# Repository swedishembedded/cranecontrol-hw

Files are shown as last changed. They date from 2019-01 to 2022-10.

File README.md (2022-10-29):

# CraneControl Schematic and PCB

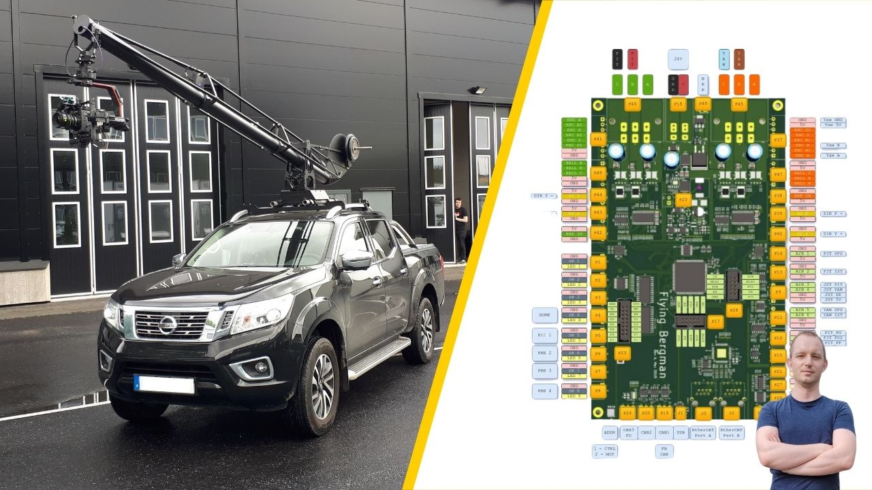
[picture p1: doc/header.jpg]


**Electronic hardware for controlling a vehicle mounted movie production crane**

	Copyright (c) 2019-2022 Martin Schröder, All rights reserved.

- Connect with me on LinkedIn: https://www.linkedin.com/in/martinschroder/
- Connect by email: martin.schroder@swedishembedded.com

This repository contains electical schematic and pcb layouts for boards that
can be used to control a movie production camera crane.

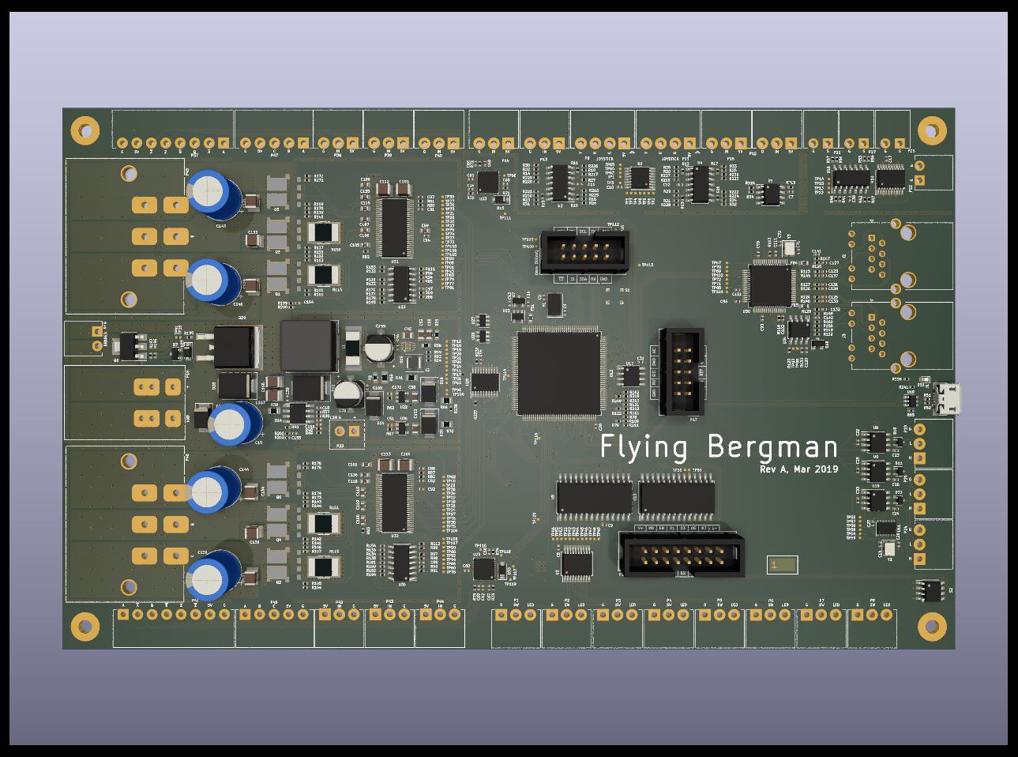
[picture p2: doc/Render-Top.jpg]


What does such a crane look like in practice? Well here is CraneControl boards
providing HMI and dual motor control function to FlyingBergman movie production
crane (click on images to watch the video):

[FlyingBergman](http://www.youtube.com/watch?v=k-2InPx5LMA
"FlyingBergman")

[FlyingBergman](http://www.youtube.com/watch?v=5sOf54V7gs8
"FlyingBergman on land")

[FlyingBergman](http://www.youtube.com/watch?v=lv9wT3cRuf8
"FlyingBergman at sea")

[FlyingBergman](https://flyingbergman.se) crane is best known for being used for filming all car scenes in
2022 Netflix series "Clark".

[FlyingBergman](http://www.youtube.com/watch?v=Xm6EU1w8b1s
"Clark")

If you are a movie producer and would like to order finished product then send
an email to info@swedishembedded.com and ask for more information. The complete
FlyingBergman setup also includes the crane assembly, HMI control panel for
mounting inside the vehicle and all necessary electronics.

## CraneControl platform

FlyingBergman is only one specific application of crane control hardware
design. CraneControl was originally designed to be a versatile solution capable
of advanced features like field oriented control of 2 60V PMSM motors at the
same time using the same microcontroller. It was also designed to provide
modern communication options like CAN-FD and EtherCAT.

In the case of FlyingBergman only a subset of these features was used - meaning
there is a lot of room to epand the use of this hardware for achieving more
complex control tasks in an industrial environment.

## Block diagram

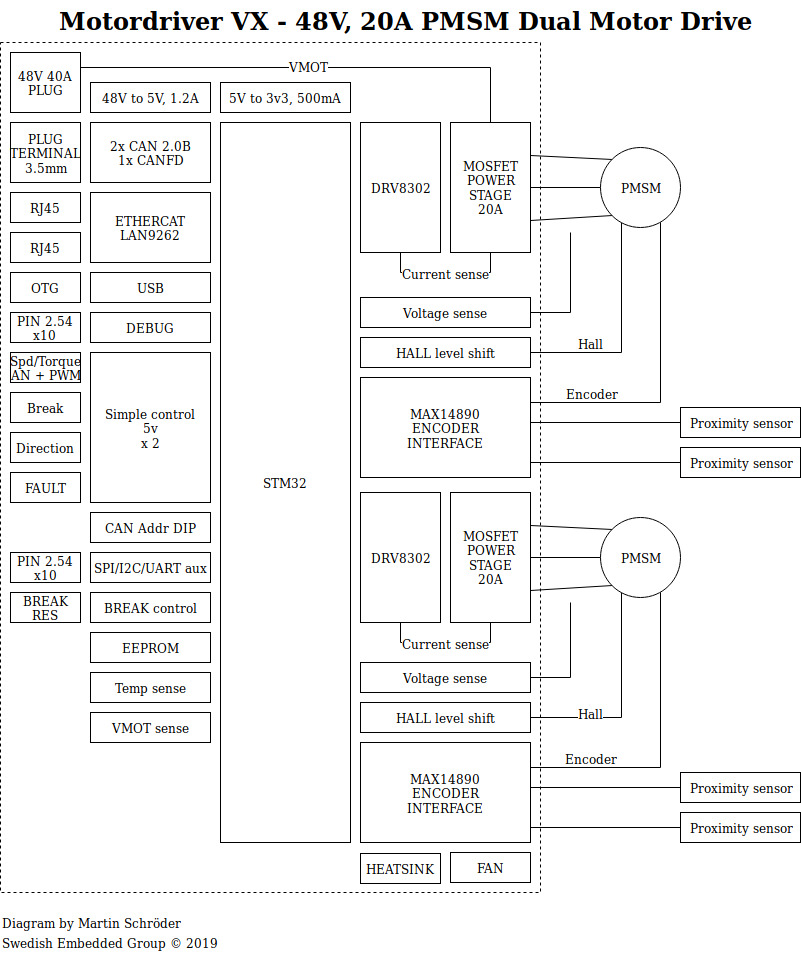
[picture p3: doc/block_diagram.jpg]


## Schematic PDF

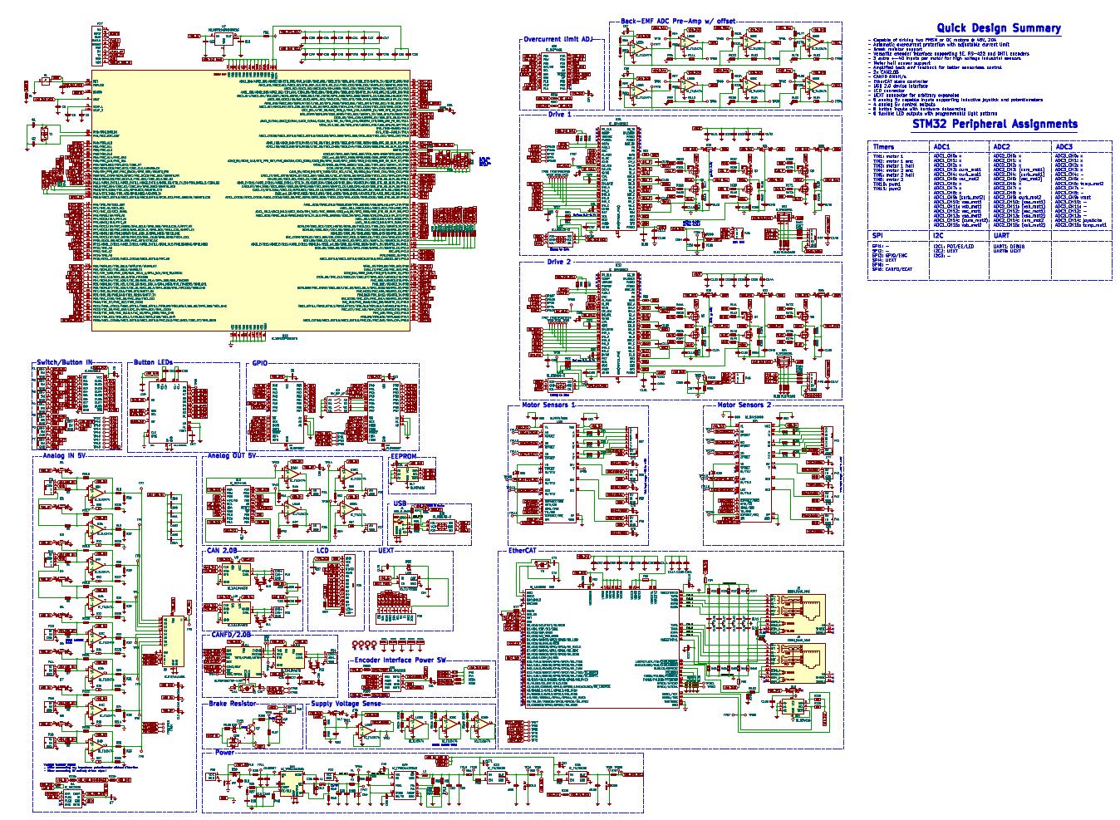
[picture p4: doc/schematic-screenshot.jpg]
Schematic


## Who is this for

This repository is for you if:

- You are a student of embedded systems courses at swedishembedded.com
  (https://swedishembedded.com/tag/training).

- You are building industrial control solutions and you would like to add
  support for advanced motor control (in this case you can also contract this
  task to Swedish Embedded Consulting Group. Book a call here:
  https://swedishembedded.com/book-call)

- You are simply curious about designing practical hardware and would like to
  learn from this project.

## License

You may use this design as inspiration for other designs as long as you develop
schematic and layout by yourself. You may also use this design as learning
materials for study.

If you would like to build a commercial product using this design then you can
contract Swedish Embedded Consulting Group to implement a specialized
hardware/software solution for you (send and email to
info@swedishembedded.com).

## Building

To generate gerbers for this design from command line you can use kibot
(https://github.com/INTI-CMNB/KiBot) with provided 'motordriver-2x.kibot.yaml'
file in this repository.

You can also edit this design in KiCad (version 6.0 or above).

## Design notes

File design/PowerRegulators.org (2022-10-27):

#+TITLE: PowerRegulators

* Main power regulator
This regulator is designed to handle up to 60V power input.

#+BEGIN_SRC octave :results output
% TPS54360 design

vout = 12;
vin = 60;
iout = 3.5;
rls = 10e3;
rdc = 36.8e-3;
vstart = 17;
vstop = 14;
lo = 33e-6;
dcj = 380e-12;
voripple = 0.005;
cout = 100e-6;
resr = 25e-3;
ioh = 2.625;
iol = 0.875;
fsw_chosen = 1500e3;
cin = 4.4e-6;
vf = 0.81;
rt_chosen = 137e3;

rdson = 92e-3;
dmax = 0.9;
i1 = 1.2e-6;
ihys = 3.4e-6;
vena = 1.2;
fdiv = 8;
voutsc = 0.1;
ton = 135e-9;
icl = 4.7;
kind = 0.3;
diout = 1.75;
dvout = 0.02;
vpeak = dvout + vout;
vi = vout;
gmps = 12;
gmea = 350e-6;
vref = 0.8;

% equation 1
vin_min = (vout + vf + rdc + iout)/0.99 + rdson * iout - vf;
% equation 2
vout_max = dmax * (vin_min - iout * rdson + vf) - vf + iout * rdc;
% equation 3
rhs = rls * (vout - vref)/vref;
% equation 4
ruvloh = (vstart - vstop)/ihys;
% equation 5
ruvlol = vena / ((vstart - vena)/ruvloh + i1);
% equation 7
rt_fsw_chosen = 1000 * 101756 / ((fsw_chosen / 1000) ^ 1.008);
rt = rt_chosen;
% equation 8
fsw = 1000 * 92417 / ((rt / 1000) ^ 0.991);
% equation 6
tss = 1024 / fsw;
% equation 9
fsw_max_skip = (1/ton) * ((iout * rdc + vout + vf)/(vin - iout * rdson + vf));
% equation 10
fsw_shift = (fdiv / ton) * ((icl * rdc + voutsc + vf)/(vin - icl * rdson + vf));
% equation 11
lo_min = ((vin - vout)/(iout * kind)) * (vout / (vin * fsw));
iripple = (vout * (vin - vout))/(vin * lo * fsw);
il_rms = sqrt(iout ^ 2 + 1/12 * ((vout * (vin - vout)) / (vin * lo * fsw))^2);
il_peak = iout + iripple / 2;
cout_min_1 = (2 * diout)/(fsw * dvout);
cout_min_2 = lo * (ioh ^ 2 - iol ^ 2)/(vpeak ^ 2 - vi ^ 2);
cout_min_3 = (1 / (fdiv * fsw)) * 1 / ((vout * voripple) / iripple);
cout_min = min([cout_min_1, cout_min_2, cout_min_3]);
resr_max = (vout * voripple) / iripple;
icout = (vout * (vin - vout))/(sqrt(12) * vin * lo * fsw);
pd = ((vin - vout) * iout * vf) / vin + (dcj * fsw * (vin + vf)^2)/2;
icirms = iout * sqrt((vout / vin_min) * (vin_min - vout)/vin_min);
dvin = (iout * 0.25)/(cin * fsw);

% equation 13
fp = iout / (2 * pi * vout * cout);
% equation 14
fz = 1 / (2 * pi * resr * cout);
fco_1 = sqrt(fp * fz);
fco_2 = sqrt(fp * fsw / 2);
fco = min(fco_1, fco_2);

r4 = ((2 * pi * fco * cout)/gmps) * (vout / (vref * gmea));
c5 = 1 / (2 * pi * r4 * fp);
c8_1 = (cout * resr) / r4;
c8_2 = 1 / (r4 * fsw * pi);
c8 = max(c8_1, c8_2);

printf('Rt for frequency %.2f: %.2f\n', fsw_chosen, rt_fsw_chosen);
printf('Switching frequency: %.2f\n', fsw);
printf('Rcomp: %f.2k, Ccomp: %fnf, Ccomp2: %f.2pf\n', r4 / 1e3, c5 / 1e-9, c8 / 1e-12)
printf('Rt: %.2fk\n', rt / 1e3)
printf('Cout_min: %.2fuf\n', cout_min / 1e-6)
printf('Rhs: %.2fk, Rls: %.2fk\n', rhs / 1e3, rls / 1e3)
printf('Ruvloh: %.2fk, Ruvlol: %.2fk\n', ruvloh / 1e3, ruvlol / 1e3)

#+END_SRC

#+RESULTS:
: Rt for frequency 1500000.00: 63982.33
: Switching frequency: 705117.97
: Rcomp: 12.198751.2k, Ccomp: 28.105922nf, Ccomp2: 204.939015.2pf
: Rt: 137.00k
: Cout_min: 1.22uf
: Rhs: 140.00k, Rls: 10.00k
: Ruvloh: 882.35k, Ruvlol: 62.81k

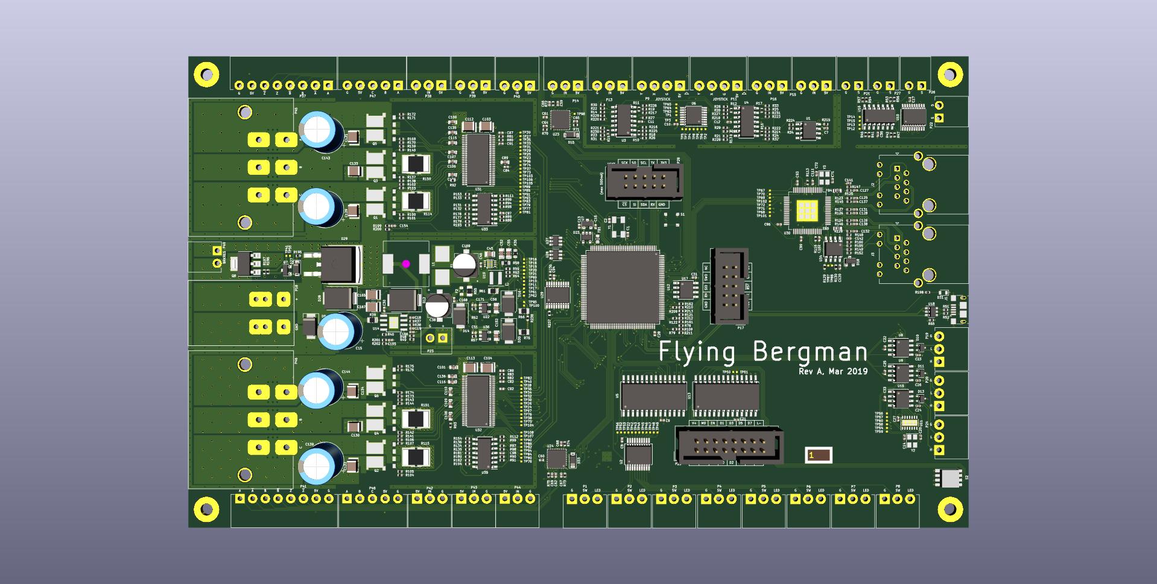
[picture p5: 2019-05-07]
doc/motordriver-2x.jpg

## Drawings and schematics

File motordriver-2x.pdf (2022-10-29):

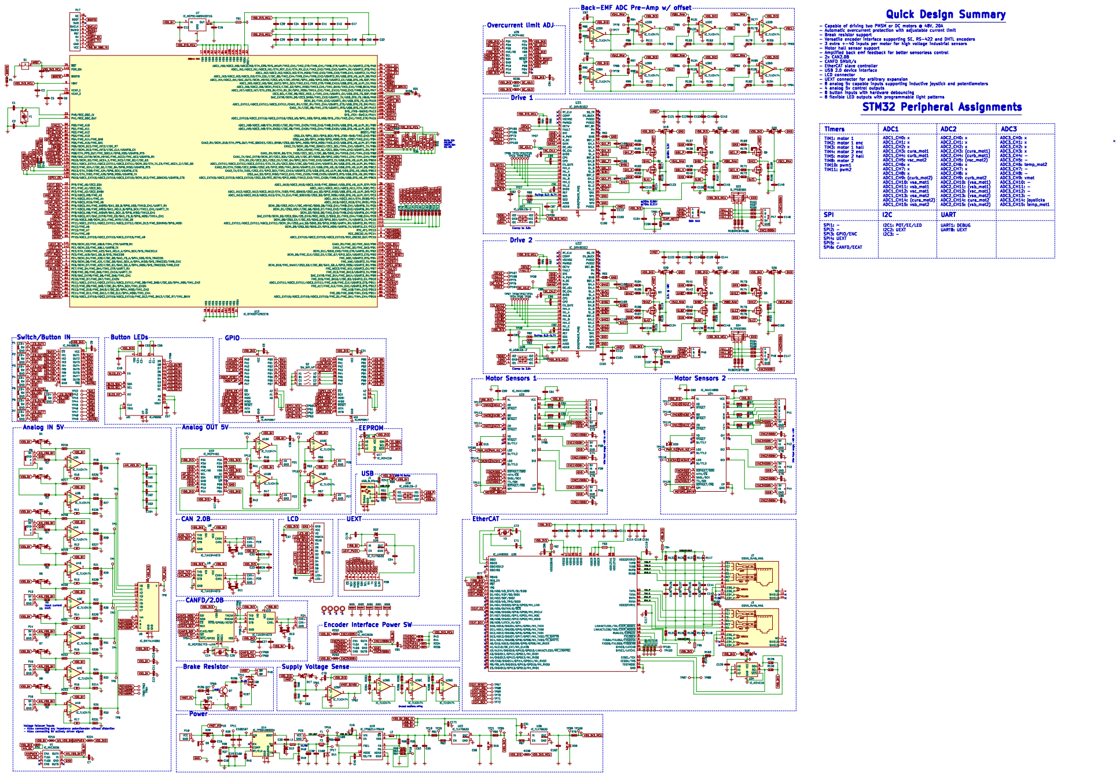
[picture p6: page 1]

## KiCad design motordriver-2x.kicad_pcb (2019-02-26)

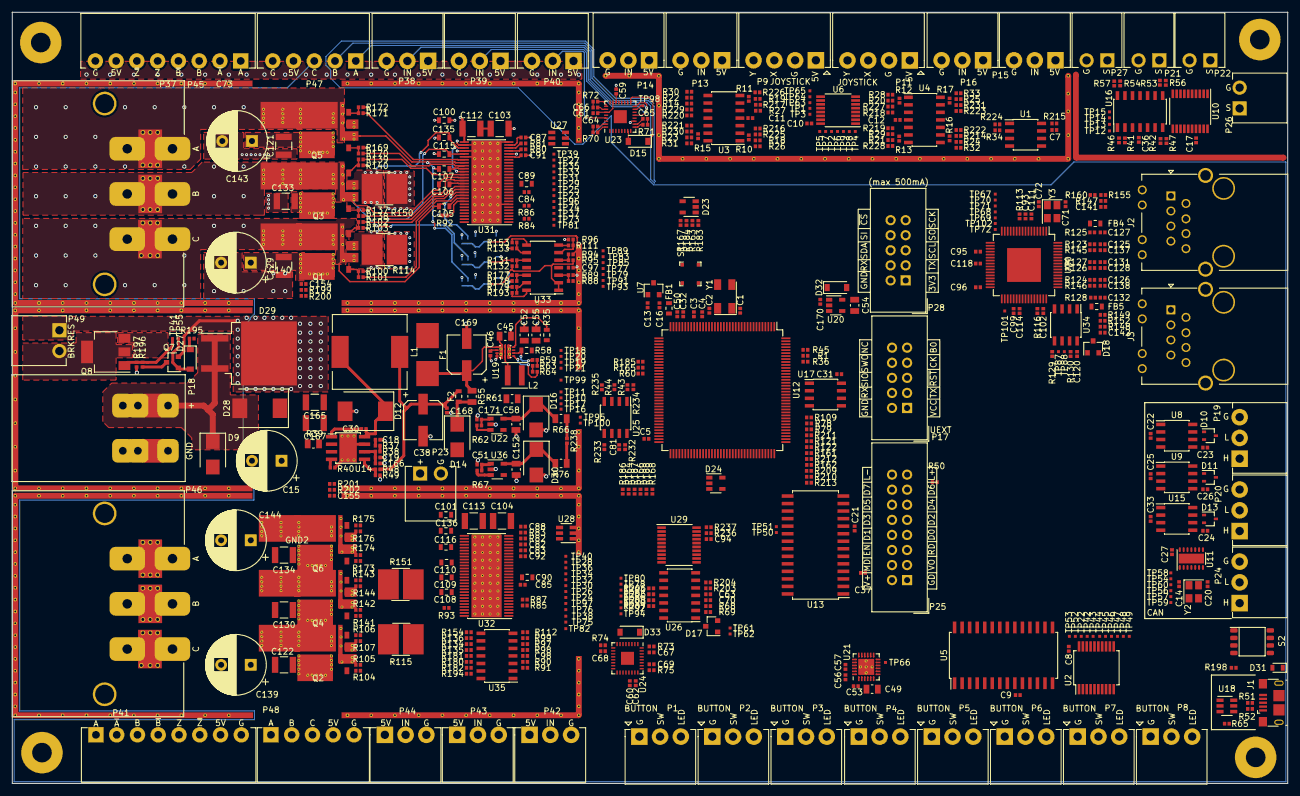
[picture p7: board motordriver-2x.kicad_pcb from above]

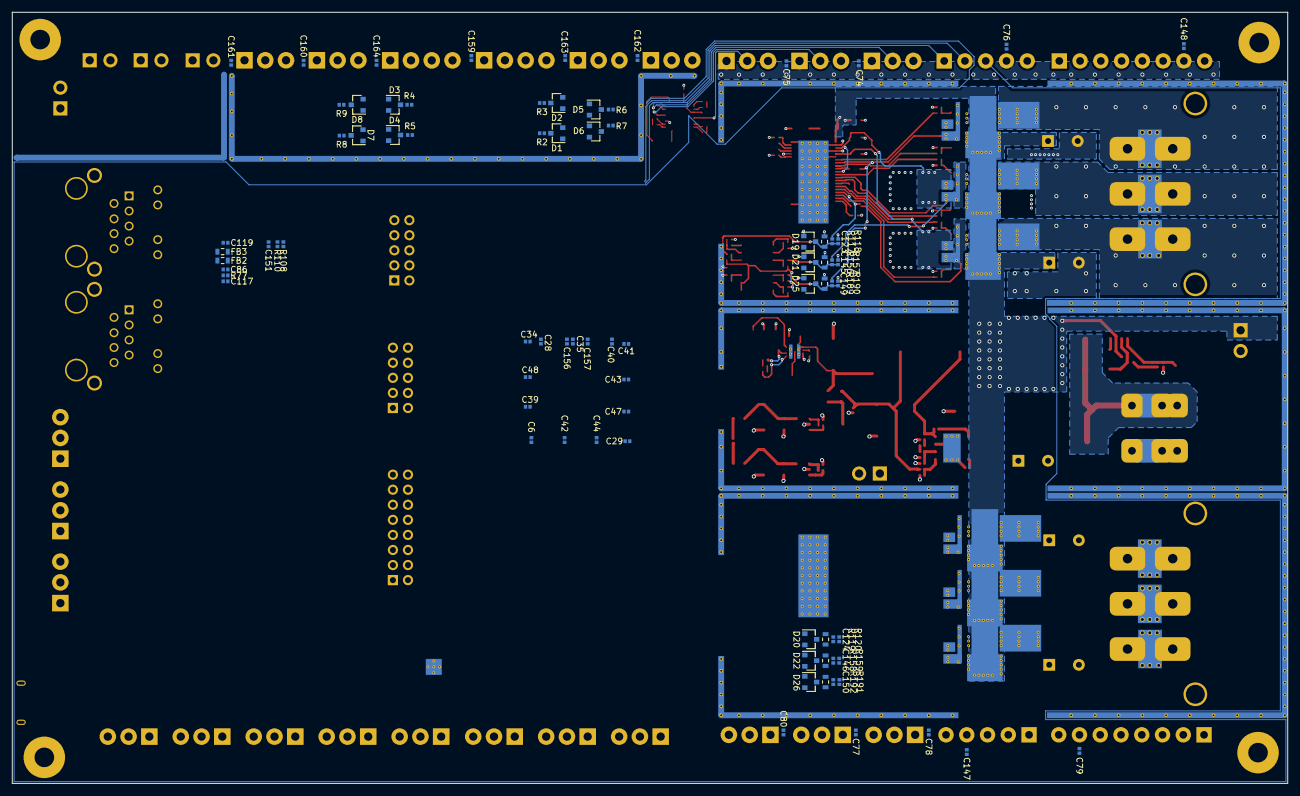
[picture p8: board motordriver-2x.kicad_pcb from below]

Board: 4 copper layers, 215.0 x 130.0 mm, 651 parts (79 on the bottom side), 453 nets.

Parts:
C1, C2, C14, C20, C71, C72, C125, C126, C127, C128, C131, C132, C137, C138: CAP_10pF_50V_0402; C_0402_1005Metric
C3, C4, C8, C9, C10, C11, C12, C16, C17, C21, C22, C23, C24, C25, C26, C27, C28, C29, C30, C31, C32, C33, C34, C35, C36, C39, C40, C41, C42, C43, C44, C46, C47, C48, C50, C59, C60, C61, C62, C63, C70, C82, C83, C86, C93, C94, C95, C96, C97, C98, C99, C102, C111, C114, C117, C118, C119, C120, C151, C154, C155, C156, C157: CAP_100nF_50V_0402; C_0402_1005Metric
C5, C6, C7, C13, C37, C51, C53, C56, C57, C73, C74, C75, C76, C77, C78, C79, C80, C81, C84, C85, C87, C88, C91, C92, C147, C148, C159, C160, C161, C162, C163, C164, C168, C170, C171: CAP_2.2uF_16V_0402; C_0402_1005Metric
C15, C139, C140, C143, C144: CAPP_220uF_63V_10x15_THT; CP_Radial_D10.0mm_P5.00mm
C18: CAP_27nF_16V_0402; C_0402_1005Metric
C19, C64, C65, C66, C67, C68, C69, C166: CAP_100pF_50V_0402; C_0402_1005Metric
C38, C169: CAPP_100uF_25V_6357; CP_Elec_6.3x5.7
C45, C49: CAP_10uF_25V_0805; C_0805_2012Metric
C52, C54, C55, C58, C152: CAP_22uF_10V_0805; C_0805_2012Metric
C89, C90: CAP_0.022uF_100V_0603; C_0603_1608Metric
C100, C101, C105, C106, C107, C108, C109, C110, C123, C124, C145, C146, C149, C150: CAP_100nF_100V_0603; C_0603_1608Metric
C103, C104, C112, C113, C121, C122, C129, C130, C133, C134, C165, C167: CAP_2.2uF_100V_1210; C_1210_3225Metric
C115, C116, C135, C136: CAP_1nF_100V_0603; C_0603_1608Metric
C141, C142: CAP_22nF_50V_0402; C_0402_1005Metric
D1, D2, D3, D4, D5, D6, D7, D8, D17, D18, D19, D20, D21, D22, D25, D26: D_BAT54S; SOT-23
D9: D_SMBJ48A; D_SMB
D10, D11, D13: D_ESDCAN03; SOT-323_SC-70
D12, D28: D_CDBC5100; D_SMC
D14: D_SMBJ12A; D_SMB
D15, D27, D32, D33: D_BAT54; D_SOD-123
D16, D30: D_SZ1SMB5913BT3G; D_SMB
D23, D24: D_TPD3E001; SOT-23-5
D29: D_STPS41H100; TO-263-2
D31: LED_RED_0603; LED_0603_1608Metric
F1: FUSE_3A_9750; Fuse_Littlefuse_9750
F2: FUSE_4A_0603; Fuse_0603_1608Metric
FB1, FB2, FB3, FB4, FB5: LB_220R_2A_0603; L_0603_1608Metric
GND1: GND_100X30
GND2, GND3: GND_MOTOR_DRIVER
GND4: GND_ANALOG_IN
GND5: GND_ANALOG_OUT
J1: USB_B_Micro; USB_Micro-B_GCT_USB3076-30-A
J2, J3: CONN_RJ45_MAG; RJ45_Tranformer
L1: L_33uH_4.2A_45mR; L_Wuerth_WE-PD-Typ-LS_1250x1250
L2: L_2.2uH_8A; L_Coilcraft_XxL4020
MT1, MT2, MT3, MT4: MOUNT_HOLE; MountingHole_3.2mm_M3_Pad
P1, P2, P3, P4, P5, P6, P7, P8: CONN_BUTTON
P9, P11: CONN_JOYSTICK
P13, P14, P15, P16, P38, P39, P40, P42, P43, P44: CONN_SENSOR
P17: CONN_DEBUG_2R; IDC-Header_2x05_P2.54mm_Vertical
P18: CONN_POWER_41A; PhoenixContact_Power41A_2,5_2-G-7,62_1x02_P7.62mm_Horizontal
P19, P20, P24: CONN_CAN
P21, P22, P26, P27: CONN_AN_OUT
P23: CONN_POWER_10A
P25: CONN_LCD
P28: CONN_UEXT
P37, P41: CONN_ENCODER
P45, P46: CONN_MOTOR; ANYTEK_7.62mm_2x_3P_32A
P47, P48: CONN_HALL
P49: CONN_BRKRES
Q1, Q2, Q3, Q4, Q5, Q6: Q_NMOS_2X_60V_63A; PowerPack-8x8-Dual
Q7: Q_PNP_BC856; SOT-23
Q8: Q_NMOS_BUK9875; SOT-223
R1, R2, R3, R4, R5, R6, R7, R8, R9, R38, R41, R42, R43, R44, R49, R53, R54, R60, R62, R63, R64, R67, R84, R85, R86, R87, R88, R89, R90, R91, R94, R95, R96, R97, R98, R99, R100, R103, R104, R107, R108, R110, R113, R116, R118, R120, R131, R132, R133, R134, R135, R136, R137, R140, R141, R144, R149, R157, R159, R160, R169, R172, R173, R176, R177, R178, R179, R180, R181, R182, R183, R184, R185, R186, R187, R188, R190, R192, R195, R196, R197, R199, R201, R203, R204, R205, R206, R207, R208: RES_10K_1%_0402; R_0402_1005Metric
R10, R11, R12, R13, R14, R15, R16, R17, R65, R147, R148: RES_0R_0402; R_0402_1005Metric
R18, R19, R20, R21, R22, R23, R24, R25: RES_1K5_1%_0402; R_0402_1005Metric
R26, R27, R28, R29, R30, R31, R32, R33, R36, R37, R45, R59, R80, R81, R82, R83, R129, R130: RES_3K_1%_0402; R_0402_1005Metric
R34, R214, R215, R216, R217, R218, R219, R220, R221, R222, R223, R224, R225, R226, R227, R228, R229, R230, R231, R232, R233, R234, R235, R236, R237, R238: RES_NOFIT_0402; R_0402_1005Metric
R35, R58: RES_147k_1%_0603; R_0603_1608Metric
R39, R55, R61, R66, R76: RES_10mOhm_1%; R_0805_2012Metric
R40, R48, R68, R117, R119, R156, R158, R189, R191: RES_137K_1%_0402; R_0402_1005Metric
R46, R47, R56, R57, R69, R111, R112, R153, R154, R163, R164, R165, R166, R167, R168, R193, R194: RES_5K_1%_0402; R_0402_1005Metric
R50, R198: RES_470R_1%_0402; R_0402_1005Metric
R51, R52, R101, R102, R105, R106, R138, R139, R142, R143, R170, R171, R174, R175: RES_22R_1%_0402; R_0402_1005Metric
R70, R71, R72, R73, R74, R75, R78, R79, R109, R121, R122, R152, R155, R161, R162, R209, R210, R211, R212, R213: RES_270R_1%_0402; R_0402_1005Metric
R77: RES_12.1K_1%_0402; R_0402_1005Metric
R92, R93: RES_1M_1%_0402; R_0402_1005Metric
R114, R115, R150, R151: RES_5mR_1%_10W; R_2818_7146Metric
R123, R124, R125, R126, R127, R128, R145, R146: RES_49.9_0.1%_0402; R_0402_1005Metric
R200, R202: RES_NTC_10K_402; R_0402_1005Metric
S1: SW_BTN_3.7x3.7; SW_PTS540
S2: SW_DIP_4P; SOIC127P670X145-8N
TP1, TP2, TP3, TP4, TP5, TP6, TP7, TP8, TP9, TP10, TP11, TP12, TP13, TP14, TP15, TP16, TP17, TP18, TP19, TP20, TP21, TP22, TP23, TP24, TP25, TP26, TP27, TP28, TP29, TP30, TP31, TP32, TP33, TP34, TP35, TP36, TP37, TP38, TP39, TP40, TP41, TP42, TP43, TP44, TP45, TP46, TP47, TP48, TP49, TP50, TP51, TP52, TP53, TP54, TP55, TP56, TP57, TP58, TP59, TP60, TP61, TP62, TP63, TP64, TP65, TP66, TP67, TP68, TP69, TP70, TP71, TP72, TP73, TP74, TP75, TP76, TP77, TP78, TP79, TP80, TP81, TP82, TP83, TP84, TP85, TP86, TP87, TP88, TP89, TP90, TP91, TP92, TP93, TP94, TP95, TP96, TP97, TP98, TP99, TP100, TP101, TP102: Test_Point; TestPoint_Pad_0.5x0.5mm
U1, U25: IC_MIC2026; SOIC-8_3.9x4.9mm_P1.27mm
U2: IC_MAX6818; SSOP-20_5.3x7.2mm_P0.65mm
U3, U4, U16, U26, U33, U35: IC_TLV2474; SOIC-14_3.9x8.7mm_P1.27mm
U5, U13: IC_MCP23S17; SOIC-28W_7.5x17.9mm_P1.27mm
U6: IC_SN74LV4051; TSSOP-16_4.4x5mm_P0.65mm
U7: IC_NCP51460SN33T1G; SOT-23
U8, U9, U15: IC_TJA1044GT3; SOIC-8_3.9x4.9mm_P1.27mm
U10, U29: IC_MCP4461; TSSOP-20_4.4x6.5mm_P0.65mm
U11: IC_MCP2517FD-xJHA; DFN-14-1EP_3x4.5mm_P0.65mm_EP1.65x4.25mm
U12: IC_STM32F429ZET6; LQFP-144_20x20mm_P0.5mm
U14: IC_TPS54360DDA; TI_SO-PowerPAD-8
U17, U34: IC_M24C16; SOIC-8_3.9x4.9mm_P1.27mm
U18, U27, U28: IC_USBLC6-2; SOT-23-6L
U19: IC_TPS62147RGXR; RGX_VQFN-11
U20, U22, U36: IC_TLV75533; SOT-23-5
U21: IC_LP55231; WQFN-24-1EP_4x4mm_P0.5mm_EP2.7x2.7mm_Thermal
U23, U24: IC_MAX14890; QFN-32-1EP_5x5mm_P0.5mm_EP2.20x2.20mm
U30: IC_LAN9252; TQFP-64-1EP_10x10mm_P0.5mm_EP5.7x5.7mm
U31, U32: IC_DRV8302; HTSSOP-56-PowerPAD_6.2x14.1mm_P0.5mm_EP3.61x6.35mm
Y1: XTAL_8Mhz_5032; Crystal_ABM3B_5032-4Pin_5.0x3.2mm
Y2: XTAL_20MHz_3225; Crystal_SMD_3225-4Pin_3.2x2.5mm
Y3: XTAL_25MHz_3225; Crystal_SMD_3225-4Pin_3.2x2.5mm

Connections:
AINPWEN: R224.2, U1.1, U12.12
AIN_OC: R34.1, U1.2, U5.21
AIN_VDD_5V: C159.1, C160.1, C161.1, C162.1, C163.1, C164.1, P9.1, P11.1, P13.1, P14.1, P15.1, P16.1, R215.1, U1.8
AP_RESET1: U5.25, U10.15
AP_SCL1: R45.1, U10.5, U12.139, U17.6, U21.9, U29.5
AP_SDA1: R36.1, U10.6, U12.137, U17.5, U21.8, U29.6
AP_WP1: U5.24, U10.14
BLED_EN: U12.58, U21.5
BLED_INT: U12.67, U21.7
BOOT0: P17.9, R1.2, U12.138
CANFD_CS: TP60.1, U11.13, U12.125
CANFD_INT: TP59.1, U11.4, U12.124
CANFD_MISO: TP70.1, U11.12, U12.127, U30.13
CANFD_MOSI: TP69.1, U11.11, U12.129, U30.17
CANFD_SCK: TP72.1, U11.10, U12.128, U30.19
CANFD_SOF: U11.3, U12.93
CAN_RX1: U8.4, U12.114
CAN_RX2: U9.4, U12.73
CAN_TX1: U8.1, U12.115
CAN_TX2: U9.1, U12.74
DC_CAL1: TP74.1, U12.89, U31.12
DC_CAL2: TP76.1, U12.90, U32.12
ECAT_CS: TP71.1, U12.126, U30.50
ECAT_IRQ: TP68.1, U12.92, U30.44
ECAT_RESET: TP67.1, U12.91, U30.11
EE_WEN: U12.140, U17.7
ENC1VDD5V: C73.2, C74.2, C75.2, C76.2, C148.1, P37.7, P38.1, P39.1, P40.1, P47.4, R232.1, U25.8
ENC2VDD5V: C77.2, C78.2, C79.2, C80.2, C147.1, P41.7, P42.1, P43.1, P44.1, P48.4, R233.1, U25.5
ENCA1: U12.110, U23.1
ENCA2: U12.81, U24.1
ENCB1: U12.133, U23.8
ENCB2: U12.82, U24.8
ENCCS1: U12.118, U23.4
ENCCS2: U12.86, U24.4
ENCMISO1: R121.1, U23.3
ENCMISO2: R122.1, U24.3
ENCMOSI1: R162.1, U23.6
ENCMOSI2: R209.1, U24.6
ENCOC1: R43.2, U5.22, U25.2
ENCOC2: R44.2, U5.23, U25.3
ENCPWEN1: R234.2, U12.69, U25.1
ENCPWEN2: R235.2, U12.70, U25.4
ENCSCK1: R78.1, U23.5
ENCSCK2: R79.1, U24.5
ENCSH1: U12.119, U23.28
ENCSH2: U12.80, U24.28
ENCZ1: U12.77, U23.24
ENCZ2: U12.85, U24.24
EN_GATE1: TP96.1, U12.117, U31.16
EN_GATE2: TP97.1, U12.116, U32.16
FAULT1: R86.1, U12.122, U31.6
FAULT2: R87.1, U12.123, U32.6
GA1_N: R102.2, U31.45
GA1_P: R101.2, U31.47
GAIN1: TP73.1, U12.53, U31.10
GAIN2: TP75.1, U12.55, U32.10
GB1_N: R139.2, U31.40
GB1_P: R138.2, U31.42
GC1_N: R171.2, U31.35
GC1_P: R170.2, U31.37
GHA2: R105.2, U32.47
GHB2: R142.2, U32.42
GHC2: R174.2, U32.37
GLA2: R106.2, U32.45
GLB2: R143.2, U32.40
GLC2: R175.2, U32.35
GND: C1.2, C2.2, C3.2, C4.2, C5.2, C6.2, C7.2, C8.2, C9.2, C10.1, C11.1, C12.1, C13.2, C14.1, C15.2, C16.2, C17.1, C18.2, C19.2, C20.2, C21.2, C22.1, C23.1, C24.1, C25.1, C26.1, C27.1, C28.2, C29.2, C31.1, C32.2, C33.2, C34.2, C35.2, C36.1, C37.2, C38.2, C39.2, C40.2, C41.2, C42.2, C43.2, C44.2, C45.2, C46.2, C47.2, C48.2, C49.2, C50.2, C51.1, C52.2, C54.2, C55.2, C57.2, C58.2, C59.2, C60.2, C61.2, C62.2, C63.2, C70.1, C71.1, C72.1, C73.1, C74.1, C75.1, C76.1, C77.1, C78.1, C79.1, C80.1, C81.2, C82.2, C83.2, C84.2, C85.2, C86.1, C87.2, C88.2, C91.2, C92.2, C93.2, C94.1, C95.2, C96.2, C97.1, C98.1, C99.2, C100.2, C101.2, C102.2, C103.2, C104.2, C111.2, C114.2, C115.2, C116.2, C117.1, C118.2, C119.2, C120.1, C121.2, C122.2, C123.2, C124.2, C125.1, C126.2, C127.1, C128.2, C129.2, C130.2, C131.1, C132.2, C133.2, C134.2, C135.2, C136.2, C137.1, C138.2, C139.2, C140.2, C141.2, C142.1, C143.2, C144.2, C145.2, C146.2, C147.2, C148.2, C149.2, C150.2, C151.2, C152.2, C154.1, C155.1, C156.1, C157.1, C159.2, C160.2, C161.2, C162.2, C163.2, C164.2, C165.2, C166.2, C167.2, C168.2, C169.2, C170.2, C171.1, D1.1, D2.1, D3.1, D4.1, D5.1, D6.1, D7.1, D8.1, D9.2, D10.3, D11.3, D12.2, D13.3, D14.2, D16.2, D17.1, D19.1, D20.1, D21.1, D22.1, D23.3, D24.3, D25.1, D26.1, D30.2, D31.1, GND1.1, GND2.1, GND3.1, GND4.1, GND5.1, J1.5, J1.6, J2.8, J2.9, J3.8, J3.9, P1.1, P2.1, P3.1, P4.1, P5.1, P6.1, P7.1, P8.1, P9.2, P11.2, P13.3, P14.3, P15.3, P16.3, P17.2, P18.2, P19.3, P20.3, P21.2, P22.2, P23.2, P24.3, P25.1, P25.16, P26.2, P27.2, P28.2, P37.8, P38.3, P39.3, P40.3, P41.8, P42.3, P43.3, P44.3, P47.5, P48.5, Q5.3, Q6.3, Q8.3, R1.1, R26.2, R27.2, R28.2, R29.2, R30.2, R31.2, R32.2, R33.2, R40.2, R41.2, R42.2, R49.2, R53.2, R54.2, R60.2, R64.2, R69.1, R77.2, R89.1, R91.1, R92.1, R93.1, R96.2, R99.2, R100.2, R103.2, R104.2, R107.2, R108.1, R110.1, R113.1, R114.1, R115.1, R116.1, R118.1, R120.1, R133.2, R136.2, R137.2, R140.2, R141.2, R144.2, R149.1, R150.2, R151.2, R157.1, R159.1, R160.1, R169.2, R172.2, R173.2, R176.2, R179.2, R182.2, R183.1, R184.1, R185.1, R186.1, R187.1, R188.1, R190.1, R192.1, R197.2, R200.2, R202.2, R204.1, R206.1, R208.1, R214.1, R225.1, R226.1, R227.1, R228.1, R229.1, R230.1, R231.1, S1.1, S1.2, S2.1, S2.2, S2.3, S2.4, U1.6, U2.10, U3.11, U4.11, U5.10, U5.15, U5.16, U5.17, U6.6, U6.7, U6.8, U7.3, U8.2, U8.8, U9.2, U9.8, U10.3, U10.4, U10.7, U10.8, U10.13, U10.16, U10.18, U11.7, U11.15, U12.16, U12.31, U12.38, U12.51, U12.61, U12.83, U12.94, U12.107, U12.120, U12.130, U13.10, U13.15, U13.16, U13.17, U14.7, U14.9, U15.2, U16.11, U17.1, U17.2, U17.3, U17.4, U18.2, U19.3, U19.4, U19.10, U19.11, U20.2, U21.4, U21.6, U21.10, U21.20, U21.21, U21.25, U22.2, U23.11, U23.33, U24.11, U24.33, U25.6, U26.11, U27.2, U28.2, U29.3, U29.7, U29.8, U29.13, U29.16, U29.18, U30.4, U30.41, U30.65, U31.7, U31.8, U31.28, U31.30, U31.32, U31.34, U31.57, U32.7, U32.8, U32.28, U32.30, U32.32, U32.34, U32.57, U33.11, U34.1, U34.2, U34.3, U34.4, U34.7, U35.11, U36.2
GPEX_CS: U12.136, U13.11
GPEX_INTA: TP50.1, U12.21, U13.20
GPEX_INTB: TP51.1, U12.22, U13.19
GPEX_MISO: R212.1, U13.14
GPEX_MOSI: R213.1, U13.13
GPEX_RESET: U12.49, U13.18
GPEX_SCK: R211.1, U13.12
GPIO_CS: U5.11, U12.88
GPIO_INTA: TP52.1, U5.20, U12.57
GPIO_INTB: TP53.1, U5.19, U12.87
GPIO_MISO: R161.1, U5.14
GPIO_MOSI: R210.1, U5.13
GPIO_RESET: U5.18, U12.56
GPIO_SCK: R109.1, U5.12
HALL_A1: D23.1, R163.2, R183.2, U12.134
HALL_A2: D24.1, R164.2, R186.2, U12.34
HALL_B1: D23.2, R167.2, R184.2, U12.135
HALL_B2: D24.2, R166.2, R187.2, U12.35
HALL_C1: D23.4, R165.2, R185.2, U12.46
HALL_C2: D24.4, R168.2, R188.2, U12.36
INHA1: TP23.1, U12.60, U31.17
INHA2: TP24.1, U12.96, U32.17
INHB1: TP29.1, U12.64, U31.19
INHB2: TP30.1, U12.97, U32.19
INHC1: TP33.1, U12.66, U31.21
INHC2: TP34.1, U12.98, U32.21
INLA1: TP25.1, U12.59, U31.18
INLA2: TP26.1, U12.43, U32.18
INLB1: TP31.1, U12.63, U31.20
INLB2: TP32.1, U12.75, U32.20
INLC1: TP35.1, U12.65, U31.22
INLC2: TP36.1, U12.76, U32.22
LCD_D0: P25.7, U13.1
LCD_D1: P25.8, U13.2
LCD_D2: P25.9, U13.3
LCD_D3: P25.10, U13.4
LCD_D4: P25.11, U13.5
LCD_D5: P25.12, U13.6
LCD_D6: P25.13, U13.7
LCD_D7: P25.14, U13.8
LCD_EN: P25.6, U13.23
LCD_LED: R50.2, U13.24
LCD_MDATA: P25.4, U13.21
LCD_READ: P25.5, U13.22
LCD_VO: P25.3, U29.9
LED_OUT1: P1.3, U21.19
LED_OUT2: P2.3, U21.18
LED_OUT3: P3.3, U21.17
LED_OUT4: P4.3, U21.16
LED_OUT5: P5.3, U21.15
LED_OUT6: P6.3, U21.14
LED_OUT7: P7.3, U21.13
LED_OUT8: P8.3, U21.12
MOC1: U12.50, U31.9
MOC2: U12.54, U32.9
MOCP_RESET: U5.26, U29.15
MOCP_WP: U5.27, U29.14
MOTOR1_BRKIN: D15.2, U12.68, U23.7
MOTOR2_BRKIN: D33.2, U12.42, U24.7
NRST: C4.1, P17.5, S1.3, S1.4, U12.25
unnamed: C1.1, U12.23, Y1.1
unnamed: C2.1, U12.24, Y1.3
unnamed: C5.1, U12.71
unnamed: C6.1, U12.106
unnamed: C14.2, U11.5, Y2.1
unnamed: C15.1, D28.1, R39.2, TP10.1
unnamed: C18.1, R37.2
unnamed: C20.1, U11.6, Y2.3
unnamed: C30.1, D12.1, L1.1, U14.8
unnamed: C30.2, U14.1
unnamed: C32.1, C50.1, FB1.2, U12.32, U12.33
unnamed: C46.1, U19.9
unnamed: C52.1, C55.1, L2.2, R35.1, R58.1, R61.2, TP19.1, U19.6
unnamed: C53.1, U21.1
unnamed: C53.2, U21.23
unnamed: C54.1, D32.2, P28.1, U20.5
unnamed: C56.1, U21.24
unnamed: C56.2, U21.2
unnamed: C57.1, U21.22
unnamed: C58.1, D16.1, R66.2, TP21.1, U22.5
unnamed: C63.1, D17.3, R68.2, R69.2, TP61.1, U26.3
unnamed: C64.1, R70.2
unnamed: C64.2, P37.2, U23.31
unnamed: C65.1, R71.2
unnamed: C65.2, P37.4, U23.10
unnamed: C66.1, R72.2
unnamed: C66.2, P37.6, U23.26
unnamed: C67.1, R73.2
unnamed: C67.2, P41.2, U24.31
unnamed: C68.1, R74.2
unnamed: C68.2, P41.4, U24.10
unnamed: C69.1, R75.2
unnamed: C69.2, P41.6, U24.26
unnamed: C71.2, U30.1, Y3.3
unnamed: C72.2, U30.2, Y3.1
unnamed: C84.1, U31.13
unnamed: C85.1, U32.13
unnamed: C86.2, FB2.1, U30.58
unnamed: C87.1, U31.27
unnamed: C88.1, U32.27
unnamed: C89.1, U31.15
unnamed: C89.2, U31.14
unnamed: C90.1, U32.15
unnamed: C90.2, U32.14
unnamed: C91.1, U31.23
unnamed: C92.1, U32.23
unnamed: C103.1, C112.2
unnamed: C104.1, C113.2
unnamed: C105.1, U31.48
unnamed: C106.1, U31.43
unnamed: C107.1, U31.38
unnamed: C108.1, U32.48
unnamed: C109.1, U32.43
unnamed: C110.1, U32.38
unnamed: C114.1, C118.1, C151.1, FB3.2, U30.6, U30.24, U30.38
unnamed: C117.2, FB5.2, R124.2, R126.2, R128.2, R146.2, R148.1, U30.51
unnamed: C119.1, FB4.1, R123.1, R125.1, R127.1, R145.1, R147.2, U30.64
unnamed: C120.2, D18.3, U34.8
unnamed: C125.2, J2.1, R123.2, U30.62
unnamed: C126.1, J3.6, R124.1, U30.54
unnamed: C127.2, J2.3, R125.2, U30.63
unnamed: C128.1, J3.4, R126.1, U30.55
unnamed: C131.2, J2.4, R127.2, U30.60
unnamed: C132.1, J3.3, R128.1, U30.52
unnamed: C137.2, J2.6, R145.2, U30.61
unnamed: C138.1, J3.1, R146.1, U30.53
unnamed: C141.1, J2.2, J2.5, R147.1
unnamed: C142.2, J3.2, J3.5, R148.2
unnamed: C152.1, D30.1, R76.2, TP99.1, U36.5
unnamed: C165.1, C167.1, R39.1, TP11.1, U14.2
unnamed: C19.1, C166.1, R38.1, U14.6
unnamed: C38.1, C168.1, F2.2, L1.2, R48.1
unnamed: C45.1, C169.1, F1.1, R55.2, TP16.1, U19.1, U19.8
unnamed: D1.3, R2.1, R216.2, U3.3
unnamed: D2.3, R3.1, R217.2, U3.5
unnamed: D3.3, R4.1, R218.2, U4.3
unnamed: D4.3, R5.1, R219.2, U4.5
unnamed: D5.3, R6.1, R220.2, U3.10
unnamed: D6.3, R7.1, R221.2, U3.12
unnamed: D7.3, R8.1, R222.2, U4.10
unnamed: D8.3, R9.1, R223.2, U4.12
unnamed: D10.1, P19.2, U8.7
unnamed: D10.2, P19.1, U8.6
unnamed: D11.1, P20.2, U9.7
unnamed: D11.2, P20.1, U9.6
unnamed: D13.1, P24.2, U15.7
unnamed: D13.2, P24.1, U15.6
unnamed: D14.1, F2.1, R55.1, TP17.1
unnamed: D15.1, U23.17
unnamed: D27.1, R195.1
unnamed: D27.2, Q7.1, TP55.1
unnamed: D31.2, R198.2
unnamed: D33.1, U24.17
unnamed: F1.2, P23.1
unnamed: FB3.1, U30.56, U30.59
unnamed: J1.1, R65.2, U18.5
unnamed: J1.2, R52.2
unnamed: J1.3, R51.2
unnamed: J2.10, R155.1
unnamed: J3.10, R152.1
unnamed: L2.1, U19.2
unnamed: P9.3, R2.2
unnamed: P9.4, R3.2
unnamed: P11.3, R4.2
unnamed: P11.4, R5.2
unnamed: P13.2, R6.2
unnamed: P14.2, R7.2
unnamed: P15.2, R8.2
unnamed: P16.2, R9.2
unnamed: P21.1, R46.1, U16.1
unnamed: P22.1, R47.1, U16.7
unnamed: P25.15, R50.1
unnamed: P26.1, R56.1, U16.8
unnamed: P27.1, R57.1, U16.14
unnamed: P37.1, R70.1, U23.32
unnamed: P37.3, R71.1, U23.9
unnamed: P37.5, R72.1, U23.25
unnamed: P38.2, U23.16
unnamed: P39.2, U23.13
unnamed: P40.2, U23.29
unnamed: P41.1, R73.1, U24.32
unnamed: P41.3, R74.1, U24.9
unnamed: P41.5, R75.1, U24.25
unnamed: P42.2, U24.16
unnamed: P43.2, U24.13
unnamed: P44.2, U24.29
unnamed: P47.1, R163.1
unnamed: P47.2, R167.1
unnamed: P47.3, R165.1
unnamed: P48.1, R164.1
unnamed: P48.2, R166.1
unnamed: P48.3, R168.1
unnamed: P49.2, Q8.2, Q8.4
unnamed: Q1.1, R100.1, R101.1
unnamed: Q1.4, R102.1, R103.1
unnamed: Q2.1, R104.1, R105.1
unnamed: Q2.4, R106.1, R107.1
unnamed: Q3.1, R137.1, R138.1
unnamed: Q3.4, R139.1, R140.1
unnamed: Q4.1, R141.1, R142.1
unnamed: Q4.4, R143.1, R144.1
unnamed: Q5.1, R169.1, R170.1
unnamed: Q5.4, R171.1, R172.1
unnamed: Q6.1, R173.1, R174.1
unnamed: Q6.4, R175.1, R176.1
unnamed: Q7.3, R196.2
unnamed: Q8.1, R196.1, R197.1, TP41.1
unnamed: R10.1, R18.2, R216.1, R225.2, U3.1
unnamed: R10.2, U3.2
unnamed: R11.1, R19.2, R217.1, R226.2, U3.7
unnamed: R11.2, U3.6
unnamed: R12.1, R20.2, R218.1, R227.2, U4.1
unnamed: R12.2, U4.2
unnamed: R13.1, R21.2, R219.1, R228.2, U4.7
unnamed: R13.2, U4.6
unnamed: R14.1, R22.2, R220.1, R229.2, U3.8
unnamed: R14.2, U3.9
unnamed: R15.1, R23.2, R221.1, R230.2, U3.14
unnamed: R15.2, U3.13
unnamed: R16.1, R24.2, R214.2, R222.1, U4.8
unnamed: R16.2, U4.9
unnamed: R17.1, R25.2, R223.1, R231.2, U4.14
unnamed: R17.2, U4.13
unnamed: R18.1, R26.1, TP7.1, U6.13
unnamed: R19.1, R27.1, TP5.1, U6.14
unnamed: R20.1, R28.1, TP3.1, U6.15
unnamed: R21.1, R29.1, TP1.1, U6.12
unnamed: R22.1, R30.1, TP2.1, U6.1
unnamed: R23.1, R31.1, TP4.1, U6.5
unnamed: R24.1, R32.1, TP6.1, U6.2
unnamed: R25.1, R33.1, TP8.1, U6.4
unnamed: R35.2, TP18.1, U19.7
unnamed: R37.1, R38.2
unnamed: R40.1, U14.4
unnamed: R41.1, R46.2, U16.2
unnamed: R42.1, R47.2, U16.6
unnamed: R48.2, R49.1, U14.5
unnamed: R51.1, U18.6
unnamed: R52.1, U18.4
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

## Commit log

2019-01-23 Add schematic
    [_saved_motordriver-2x.sch, motordriver-2x.kicad_pcb, motordriver-2x.sch]
2019-01-23 add missing files
    [MotorDrive.xml]
2019-01-25 update schematic and add footprints
    [MotorDrive.xml, motordriver-2x.sch]
2019-01-25 update schematic
    [motordriver-2x.sch]
2019-01-26 update encoder interface
    [motordriver-2x.sch]
2019-01-27 add test points and pmic to motor drive circuit
    [motordriver-2x.sch]
2019-01-28 add analog in
    [MotorDrive.xml, motordriver-2x.sch]
2019-01-29 add can and eeprom
    [MotorDrive.xml, motordriver-2x.sch]
2019-01-29 add switch input and gpio chip
    [MotorDrive.xml, motordriver-2x.sch]
2019-01-29 add ethercat interface
    [motordriver-2x.sch]
2019-01-29 add lcd connector
    [motordriver-2x.sch]
2019-01-29 work on the ethercat circuit
    [motordriver-2x.sch]
2019-01-30 add main power
    [motordriver-2x.sch]
2019-01-30 add power supplies
    [motordriver-2x.sch]
2019-01-30 cleanup schematic
    [MotorDrive.xml, motordriver-2x.sch]
2019-01-30 start connecting pins
    [motordriver-2x.sch]
2019-01-31 connect more pins to mcu, change opamp and add analog multiplexer
    [motordriver-2x.sch]
2019-01-31 change analog out to opamp output
    [motordriver-2x.sch]
2019-01-31 add opamps to voltage sensing
    [motordriver-2x.sch]
2019-01-31 add preamp for voltage sensing and add UEXT
    [motordriver-2x.sch]
2019-02-01 add gpio and connect most pins
    [motordriver-2x.sch]
2019-02-01 update annotated schematic
    [motordriver-2x.sch]
2019-02-01 start preliminary pcb layout
    [motordriver-2x.kicad_pcb, motordriver-2x.sch]
2019-02-01 fix footprints
    [motordriver-2x.kicad_pcb, motordriver-2x.sch]
2019-02-02 add break resistor circuit and simulation
    [motordriver-2x.sch]
2019-02-02 draft sent
    [motordriver-2x.sch]
2019-02-05 start reviewing the schematic
    [motordriver-2x.kicad_pcb, motordriver-2x.sch]
2019-02-11 review start
    [_saved_motordriver-2x.sch, motordriver-2x.kicad_pcb, motordriver-2x.sch]
2019-02-11 continue schematic review: capacitors
    [motordriver-2x.sch]
2019-02-11 review diodes
    [motordriver-2x.sch]
2019-02-14 schematic review
    [motordriver-2x.sch]
2019-02-14 review footprints for switches and sensors
    [motordriver-2x.sch]
2019-02-15 component level review almost done on connectors
    Add a bunch of modified footprints and push latest schematic
    [motordriver-2x.sch]
2019-02-15 review most of the resistors
    [motordriver-2x.sch]
2019-02-15 finish resistor review
    [motordriver-2x.sch]
2019-02-16 ic review
    [motordriver-2x.sch]
2019-02-17 review power, eeprom and can txc
    [motordriver-2x.sch]
2019-02-17 review usb
    [motordriver-2x.sch]
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2019-02-18 review power regulators
    [motordriver-2x.sch, motordriver-2x.xml]
2019-02-18 component review done
    [motordriver-2x.sch]
2019-02-19 review labels
    [motordriver-2x.sch]
2019-02-19 finish review and drc
    [motordriver-2x.sch]
2019-02-19 update field values
    [motordriver-2x.sch]
2019-02-19 start component placement
    [motordriver-2x.kicad_pcb, motordriver-2x.sch]
2019-02-20 pcb layout
    [motordriver-2x.kicad_pcb, motordriver-2x.sch]
2019-02-20 optimize connector size
    [motordriver-2x.kicad_pcb, motordriver-2x.sch]
2019-02-20 place second motor driver
    [motordriver-2x.kicad_pcb]
2019-02-21 review footprints and horizontal vertical stuff
    [motordriver-2x.kicad_pcb, motordriver-2x.sch]
2019-02-21 power supply layout
    [motordriver-2x.kicad_pcb, motordriver-2x.sch]
2019-02-21 cpu layout
    [motordriver-2x.kicad_pcb]
2019-02-21 save latest schematic
    [motordriver-2x.kicad_pcb, motordriver-2x.sch]
2019-02-22 come up with pcb outline
    [motordriver-2x.kicad_pcb, motordriver-2x.sch, motordriver-2x.xml]
2019-02-22 better placement
    [motordriver-2x.kicad_pcb, motordriver-2x.sch]
2019-02-22 create custom grounds
    [motordriver-2x.kicad_pcb, motordriver-2x.sch]
2019-02-23 update grounds and connectors
    [motordriver-2x.kicad_pcb]
2019-02-25 start routing
    [motordriver-2x.kicad_pcb]
2019-02-25 routing with fills
    [motordriver-2x.kicad_pcb]
2019-02-25 fix many routing issues
    [motordriver-2x.kicad_pcb, motordriver-2x.sch]
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2019-02-26 continue layout of second drive
    [motordriver-2x.sch]
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2019-02-27 fix rj45 and route ethercat
    [motordriver-2x.sch]
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2019-02-28 continue layout of cpu
    [motordriver-2x.sch]
2019-03-01 rewire bunch of control lines
    [motordriver-2x.sch, motordriver-2x.xml]
2019-03-01 down to 35 unrouted nets
    [motordriver-2x.sch]
2019-03-01 down to 14 unrouted
    [motordriver-2x.sch]
2019-03-02 everything connected and courtyards updated
    [motordriver-2x.sch]
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2019-03-07 update board to have proper layer window
    [motordriver-2x.xml]
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2019-03-07 move all footprints to custom library and push updates to schematic and pcb
    [motordriver-2x.sch]
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2019-03-14 minor fixes
    [MotorDrive.xml, motordriver-2x-bom.csv, motordriver-2x.sch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]
2019-03-23 push fixes to pcb
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2022-10-23 kicad: update to kicad v6
    Closes #2
    [motordriver-2x.kicad_sch]
2022-10-24 ci: add kibot build support
    Closes #3
    [motordriver-2x.kibot.yaml, motordriver-2x.sch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]
2022-10-25 bom: add bom generation
    Closes #4
    [motordriver-2x.kibot.yaml, motordriver-2x.kicad_sch]
2022-10-27 cleanup: organize files and make sure we have all 3d models
    Related to #5
    [MotorDrive.xml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]
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
